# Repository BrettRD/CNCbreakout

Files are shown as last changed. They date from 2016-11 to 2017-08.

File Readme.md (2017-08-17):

# CNCbreakout

This is the working folder for the breakout board to wire the FPGA interface cards into the CNC cabinet.

The interfaces as described did not standardise voltages on the limit switches and left some signal poalrities up to chance

This board also has LED outputs showing the current state of all limits and home switches.

## PCB
There is a toner-transfer PCB in the compactus, but it requires about six hours of work fitting track jumpers.

The KiCad PCB simply has these as top-layer tracks. Export gerbers and buy PCBs; save your sanity.

## Documents:
There is no manual for the 220V X-axis servo controller. This repo contains the closest approximation, and seems to have the same menu and pinouts.

The pinouts for the interface cables currently only exist within the KiCad document.  Some of these will need to have piggyback connections.  With a bit of work and sanity checking, these pinouts can be converted to tables or PDF diagrams.

## Current Hardware:
The inactive X-axis motor has a fault in its signal lines pinout. This can be seen on the servo controller: navigate the menu to a live encoder display.  See the maxsineMotorpinout spreadsheet for the correct wiring.

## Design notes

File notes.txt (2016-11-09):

Estop handling is not required on this board.

Cables:
	Enable lines are routed via the breakout board
	Pinout not finalised
	DE15 and DE9 pcb connectors are by Oupiin available at altronics drawn from datasheet

PCB layout:
	Need to plan cable placement

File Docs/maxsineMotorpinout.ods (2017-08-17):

Signal | Motor Pin number | Colour | Diameter | Controller pin number
A+ | 4 | brown yellow | 0.25 | 1
A- | 7 | brown grey | 0.25 | 2
B+ | 5 | green brown | 0.25 | 3
B- | 8 | green black | 0.25 | 4
Z+ | 6 | white red | 0.14 | 5
Z- | 9 | white black | 0.14 | 6
U+ | 10 | black | 0.14 | 7
U- | 13 | brown | 0.14 | 8
V+ | 11 | orange | 0.14 | 9
V- | 14 | red | 0.14 | 10
W+ | 12 | green | 0.14 | 11
W- | 15 | yellow | 0.14 | 12
5v+ | 2 | brown red | 0.5 | 14
5v+ | 2 | brown red | 0.5 | 15
5v+ | 2 | brown red | 0.5 | 16
5v+ | 2 | brown red | 0.5 | 17
gnd | 3 | brown blue | 0.5 | 18
gnd | 3 | brown blue | 0.5 | 19
gnd | 3 | brown blue | 0.5 | 20
gnd | 3 | brown blue | 0.5 | 21
shield | 1 | shield |  | 26

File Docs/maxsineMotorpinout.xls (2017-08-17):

Signal | Motor Pin number | Colour | Diameter | Controller pin number
A+ | 4 | green | 0.25 | 1
A- | 7 | yellow | 0.25 | 2
B+ | 5 | orange | 0.25 | 3
B- | 8 | red | 0.25 | 4
Z+ | 6 | black | 0.14 | 5
Z- | 9 | brown | 0.14 | 6
U+ | 10 | brown yellow | 0.14 | 7
U- | 13 | brown grey | 0.14 | 8
V+ | 11 | green brown | 0.14 | 9
V- | 14 | green black | 0.14 | 10
W+ | 12 | white red | 0.14 | 11
W- | 15 | white black | 0.14 | 12
5v+ | 2 | brown red | 0.5 | 14
5v+ | 2 | brown red | 0.5 | 15
5v+ | 2 | brown red | 0.5 | 16
5v+ | 2 | brown red | 0.5 | 17
gnd | 3 | brown blue | 0.5 | 18
gnd | 3 | brown blue | 0.5 | 19
gnd | 3 | brown blue | 0.5 | 20
gnd | 3 | brown blue | 0.5 | 21
shield | 1 | shield |  | 26

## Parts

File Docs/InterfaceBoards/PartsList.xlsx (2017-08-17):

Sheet: 5i22_Baseboard Rev C x 2pcs
Ref | Value | Package | Manufacturer | Part Number | Element14 | Notes
C1 | 47uF | PANASONIC_D | Panasonic | EEEFK1C470P | 1850100
C2 | 100nF | C0805 | Multicomp | MC0603B104K500CT | 1759122 | 50V X7R dielectric 10%
C3 | 47uF | PANASONIC_D | Panasonic | EEEFK1C470P | 1850100
C4 | 100nF | C0805 | Multicomp | MC0603B104K500CT | 1759122 | 50V X7R dielectric 10%
C5 | 47uF | PANASONIC_D | Panasonic | EEEFK1C470P | 1850100
C6 | 100nF | C0805 | Multicomp | MC0603B104K500CT | 1759122 | 50V X7R dielectric 10%
C7 | 47uF | PANASONIC_D | Panasonic | EEEFK1C470P | 1850100
C8 | 100nF | C0805 | Multicomp | MC0603B104K500CT | 1759122 | 50V X7R dielectric 10%
C9 | 10nF | C1206 | Phycomp | CC1206KKX7RCBB103 | 1284146 | Must be 1000V
C10 | 47uF | PANASONIC_D | Panasonic | EEEFK1C470P | 1850100
C11 | 100nF | C0805 | Multicomp | MC0603B104K500CT | 1759122 | 50V X7R dielectric 10%
C12 | 47uF | PANASONIC_D | Panasonic | EEEFK1C470P | 1850100
C13 | 100nF | C0805 | Multicomp | MC0603B104K500CT | 1759122 | 50V X7R dielectric 10%
C14 | 100nF | C0805 | Multicomp | MC0603B104K500CT | 1759122 | 50V X7R dielectric 10%
C15 | 100nF | C0805 | Multicomp | MC0603B104K500CT | 1759122 | 50V X7R dielectric 10%
C16 | 100nF | C0805 | Multicomp | MC0603B104K500CT | 1759122 | 50V X7R dielectric 10%
C17 | 100nF | C0805 | Multicomp | MC0603B104K500CT | 1759122 | 50V X7R dielectric 10%
C18 | 100nF | C0805 | Multicomp | MC0603B104K500CT | 1759122 | 50V X7R dielectric 10%
C19 | 100nF | C0805 | Multicomp | MC0603B104K500CT | 1759122 | 50V X7R dielectric 10%
C20 | 1nF | C1206 | Multicomp | MC1206B102K102CT | 1855896 | Must be 1000V
C21 | 1nF | C1206 | Multicomp | MC1206B102K102CT | 1855896 | Must be 1000V
C22 | 1nF | C1206 | Multicomp | MC1206B102K102CT | 1855896 | Must be 1000V
C23 | 1nF | C1206 | Multicomp | MC1206B102K102CT | 1855896 | Must be 1000V
C24 | 1nF | C1206 | Multicomp | MC1206B102K102CT | 1855896 | Must be 1000V
C25 | 10nF | C1206 | Multicomp | MC1206B102K102CT | 1855896 | Must be 1000V
C26 | 1uF | C1206K | AVX | 12061C105KAT2A | 1657939 | > 50v preferred
C27 | 100nF | C0805 | Multicomp | MC0603B104K500CT | 1759122 | 50V X7R dielectric 10%
C28 | 100nF | C0805 | Multicomp | MC0603B104K500CT | 1759122 | 50V X7R dielectric 10%
C29 | 100nF | C0805 | Multicomp | MC0603B104K500CT | 1759122 | 50V X7R dielectric 10%
C30 | 100nF | C0805 | Multicomp | MC0603B104K500CT | 1759122 | 50V X7R dielectric 10%
C31 | 100nF | C0805 | Multicomp | MC0603B104K500CT | 1759122 | 50V X7R dielectric 10%
C32 | 100nF | C0805 | Multicomp | MC0603B104K500CT | 1759122 | 50V X7R dielectric 10%
C33 | 1nF | C1206 | Multicomp | MC1206B102K102CT | 1855896 | Must be 1000V
C34 | 1nF | C1206 | Multicomp | MC1206B102K102CT | 1855896 | Must be 1000V
C35 | 1nF | C1206 | Multicomp | MC1206B102K102CT | 1855896 | Must be 1000V
C36 | 1nF | C1206 | Multicomp | MC1206B102K102CT | 1855896 | Must be 1000V
C37 | 100nF | C0805 | Multicomp | MC0603B104K500CT | 1759122 | 50V X7R dielectric 10%
C38 | 100nF | C0805 | Multicomp | MC0603B104K500CT | 1759122 | 50V X7R dielectric 10%
D1 | GF1G | DO214AC | Vishay | GF1G-E3/5CA | 9549595
D2 | GF1G | DO214AC | Vishay | GF1G-E3/5CA | 9549595
D3 | GF1G | DO214AC | Vishay | GF1G-E3/5CA | 9549595
D4 | GF1G | DO214AC | Vishay | GF1G-E3/5CA | 9549595
D5 | GF1G | DO214AC | Vishay | GF1G-E3/5CA | 9549595
D6 |  | 1208-BI-COLOR | Dialight | 5988510207F | 1850756
IC1 | 74LVC32AD | SO14 | TI | SN74LVC32AD | 1102974
IC2 | 74LVC541ADW | SO20W | TI | 74LVC541ADW | 1470749
IC3 | 74LVC1G02DBV | SOT23-5 | TI | SN74LVC1G02DBVR | 1287579
IC4 | MC78M15CDT | TO252 | On Semi | MC78M15CDTG | 1211124
L1 | MPLCH0740L4R7 | 740 | Kemet | MPLCH0740L4R7 | 2364599
L2 | MPLCH0740L4R7 | 740 | Kemet | MPLCH0740L4R8 | 2364600
L3 | MPLCH0740L4R7 | 740 | Kemet | MPLCH0740L4R9 | 2364601
Q1 | STD30NF06L | TO252 | ST Micro | STD30NF06LT4 | 1752032
Q2 | STD30NF06L | TO252 | ST Micro | STD30NF06LT5 | 1752033
Q3 | MUN2211T1 | SC59-BEC | On Semi | MUN2211T1G | 1232166
Q4 | MUN2211T1 | SC59-BEC | On Semi | MUN2211T1G | 1232166
Q5 | STD30NF06L | TO252 | ST Micro | STD30NF06LT5 | 1752033
Q6 | STD30NF06L | TO252 | ST Micro | STD30NF06LT5 | 1752033
Q7 | STD30NF06L | TO252 | ST Micro | STD30NF06LT5 | 1752033
Q8 | MUN2211T1 | SC59-BEC | On Semi | MUN2211T1G | 1232166
Q9 | MUN2211T1 | SC59-BEC | On Semi | MUN2211T1G | 1232166
Q10 | MUN2211T1 | SC59-BEC | On Semi | MUN2211T1G | 1232166
R1 | 1M | R1206 |  |  |  | 5% 1206 case
R2 | 51R | R0805 |  |  |  | 1% 0.125W 0805 case
R3 | 51R | R0805 |  |  |  | 1% 0.125W 0805 case
R4 | 51R | R0805 |  |  |  | 1% 0.125W 0805 case
R5 | 51R | R0805 |  |  |  | 1% 0.125W 0805 case
R6 | 0R | R0805 |  |  |  | 1% 0.125W 0805 case
R7 | 0R | R0805 |  |  |  | 1% 0.125W 0805 case
R8 | 10k | R0805 |  |  |  | 1% 0.125W 0805 case
R9 | 10k | R0805 |  |  |  | 1% 0.125W 0805 case
R10 | 10k | R0805 |  |  |  | 1% 0.125W 0805 case
R11 | 10k | R0805 |  |  |  | 1% 0.125W 0805 case
R12 | 220R | R0805 |  |  |  | 1% 0.125W 0805 case
R13 | 220R | R0805 |  |  |  | 1% 0.125W 0805 case
R14 | 1M | R1206 |  |  |  | 5% 1206 case
R15 | 220R | R0805 |  |  |  | 1% 0.125W 0805 case
R16 | 220R | R0805 |  |  |  | 1% 0.125W 0805 case
R17 | 220R | R0805 |  |  |  | 1% 0.125W 0805 case
R18 | 1k | R0805 |  |  |  | 1% 0.125W 0805 case
R19 | 1k | R0805 |  |  |  | 1% 0.125W 0805 case
R20 | 2K | R0805 |  |  |  | 1% 0.125W 0805 case
R21 | 51R | R0805 |  |  |  | 1% 0.125W 0805 case
R22 | 2K | R0805 |  |  |  | 1% 0.125W 0805 case
R23 | 330R | R0805 |  |  |  | 1% 0.125W 0805 case
R24 | 270R | R0805 |  |  |  | 1% 0.125W 0805 case
U1 | SN74LVC2G14DBV | SOT23-6 | TI | SN74LVC2G14DBVR | 1470884
U2 | SN74LVC1G19DBV | SOT23-6 | TI | SN74LVC1G19DBVR | 2334936
U3 | SN74LVC2G14DBV | SOT23-6 | TI | SN74LVC2G14DBVR | 1470884
U4 | ACPL-302P | SO-6(P) | Avago | ACPL-P302-000E | 1640555 | Can use ACPL-P314-000E as an alternative (Element14 : 1640556)
U5 | ACPL-302P | SO-6(P) | Avago | ACPL-P302-000E | 1640555 | Can use ACPL-P314-000E as an alternative (Element14 : 1640556)
U6 | ACPL-302P | SO-6(P) | Avago | ACPL-P302-000E | 1640555 | Can use ACPL-P314-000E as an alternative (Element14 : 1640556)
U7 | ACPL-302P | SO-6(P) | Avago | ACPL-P302-000E | 1640555 | Can use ACPL-P314-000E as an alternative (Element14 : 1640556)
U8 | ACPL-302P | SO-6(P) | Avago | ACPL-P302-000E | 1640555 | Can use ACPL-P314-000E as an alternative (Element14 : 1640556)
U9 | SN74LVC2G14DBV | SOT23-6 | TI | SN74LVC2G14DBVR | 1470884
U10 | HCPL-263L | SO-8 | Avago | HCPL-263L-300E | 1085053
X1 | 2550- | PAK100/2500-50 | AMP | T821150A1S100CEU | 2215315 | Any alternative is OK
X2 | 2550- | PAK100/2500-50 | AMP | T821150A1S100CEU | 2215315 | Any alternative is OK
X3 | 641737 | 641737 | TE Connectivity | 1-641737-1 | 6478712 | Molex MATE-N-LOK hard disk connector
X4 |  | PAK100/2500-F-16 | TE Connectivity | 215307-8 | 3419241 | Any alternative is OK
X5 |  | PAK100/2500-F-16 | TE Connectivity | 215307-8 | 3419241 | Any alternative is OK
X6 | 2514-F | PAK100/2500-F-14 | TE Connectivity | 215307-7 | 3419230 | Any alternative is OK
X7 |  | PAK100/2500-F-16 | TE Connectivity | 215307-8 | 3419241 | Any alternative is OK
X8 |  | PAK100/2500-F-16 | TE Connectivity | 215307-8 | 3419241 | Any alternative is OK
X9 |  | PHOENIXCONTACT_MSTBA_508_7 | Phoenix Contact | MSTBA 2,5/ 7-G-5,08-LR | 2315187 | Get some of the screw terminal mating halves as well.
X10 |  | PHOENIXCONTACT_MSTBA-508_5 | Phoenix Contact | MSTBA 2,5/ 5-G-5,08-LR | 2315185 | Get some of the screw terminal mating halves as well.

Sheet: ACS806 Rev C x 4pcs
Ref | Value | Package | Manufacturer | Part Number | Element14 | Notes
C1 | 100nF | C0805 | Multicomp | MC0603B104K500CT | 1759122 | 50V X7R dielectric 10%
C2 | 100nF | C0805 | Multicomp | MC0603B104K500CT | 1759122 | 50V X7R dielectric 10%
C3 | 47uF | PANASONIC_C | Panasonic | EEEFK0J470R | 1850084 | Minimum 4v
C4 | 100nF | C0805 | Multicomp | MC0603B104K500CT | 1759122 | 50V X7R dielectric 10%
C5 | 22uF | PANASONIC_C | Panasonic | EEEFK1E220AR | 1244411 | Minimum 16v
C6 | 100nF | C0805 | Multicomp | MC0603B104K500CT | 1759122 | 50V X7R dielectric 10%
C7 | 100nF | C0805 | Multicomp | MC0603B104K500CT | 1759122 | 50V X7R dielectric 10%
C8 | 100nF | C0805 | Multicomp | MC0603B104K500CT | 1759122 | 50V X7R dielectric 10%
C9 | 100nF | C0805 | Multicomp | MC0603B104K500CT | 1759122 | 50V X7R dielectric 10%
C10 | 100nF | C0805 | Multicomp | MC0603B104K500CT | 1759122 | 50V X7R dielectric 10%
C11 | 100nF | C0805 | Multicomp | MC0603B104K500CT | 1759122 | 50V X7R dielectric 10%
C12 | 100nF | C0805 | Multicomp | MC0603B104K500CT | 1759122 | 50V X7R dielectric 10%
LED1 |  | CHIP-LED0805 | Multicomp | 703-0104 | 2112116 | green
LED2 |  | CHIP-LED0805 | Multicomp | 703-0107 | 2112119 | red
LED3 |  | CHIP-LED0805 | Multicomp | 703-0105 | 2112117 | yellow
R1 | 1K | R1206 |  |  |  | 1% 0.25W 1206 case
R2 | 1K | R1206 |  |  |  | 1% 0.25W 1206 case
R3 | 1K | R1206 |  |  |  | 1% 0.25W 1206 case
R4 | 10k | R0805 |  |  |  | 1% 0.125W 0805 case
R5 | 51R | R0805 |  |  |  | 1% 0.125W 0805 case
R6 | 270R | R0805 |  |  |  | 1% 0.125W 0805 case
R7 | 10k | R0805 |  |  |  | 1% 0.125W 0805 case
R8 | 51R | R0805 |  |  |  | 1% 0.125W 0805 case
R9 | 270R | R0805 |  |  |  | 1% 0.125W 0805 case
R10 | 330R | R0805 |  |  |  | 1% 0.125W 0805 case
R11 | 1K | R0805 |  |  |  | 1% 0.125W 0805 case
R12 | 470R | R0805 |  |  |  | 1% 0.125W 0805 case
R13 | 470R | R0805 |  |  |  | 1% 0.125W 0805 case
R14 | 470R | R0805 |  |  |  | 1% 0.125W 0805 case
R15 | 470R | R0805 |  |  |  | 1% 0.125W 0805 case
R16 | 470R | R0805 |  |  |  | 1% 0.125W 0805 case
R17 | 470R | R0805 |  |  |  | 1% 0.125W 0805 case
R18 | 470R | R0805 |  |  |  | 1% 0.125W 0805 case
R19 | 270R | R0805 |  |  |  | 1% 0.125W 0805 case
R20 | 51R | R0805 |  |  |  | 1% 0.125W 0805 case
R21 | 270R | R0805 |  |  |  | 1% 0.125W 0805 case
R22 | 51R | R0805 |  |  |  | 1% 0.125W 0805 case
R23 | 270R | R0805 |  |  |  | 1% 0.125W 0805 case
R24 | 51R | R0805 |  |  |  | 1% 0.125W 0805 case
R25 | 2K | R0805 |  |  |  | 1% 0.125W 0805 case
R26 | 51R | R0805 |  |  |  | 1% 0.125W 0805 case
R27 | 270R | R0805 |  |  |  | 1% 0.125W 0805 case
R28 | 51R | R0805 |  |  |  | 1% 0.125W 0805 case
R29 | 270R | R0805 |  |  |  | 1% 0.125W 0805 case
R30 | 51R | R0805 |  |  |  | 1% 0.125W 0805 case
U1 | AEIC-2631-S16 | SO16 | Avago | AEIC-2631-S16 | 2447896
U2 | ACPL-217 | SO-4 | Avago | ACPL-217-50AE | 1602616
U3 | SN74LVC2G14DBV | SOT23-6 | TI | SN74LVC2G14DBVR | 1470884
U4 | ACPL-217 | SO-4 | Avago | ACPL-217-50AE | 1602616
U5 | SN74LVC2G14DBV | SOT23-6 | TI | SN74LVC2G14DBVR | 1470884
U6 | HCPL-263L | SO-8 | Avago | HCPL-263L-300E | 1085053
U7 | SN74LVC2G14DBV | SOT23-6 | TI | SN74LVC2G14DBVR | 1470884
U8 | HCPL-263L | SO-8 | Avago | HCPL-263L-300E | 1085053
U9 | SN74LVC2G14DBV | SOT23-6 | TI | SN74LVC2G14DBVR | 1470884
U10 | HCPL-263L | SO-8 | Avago | HCPL-263L-300E | 1085053
X1 | 2516-5 | PAK100/2500-5-16 | TE Connectivity | 1-1634689-6 | 8396019
X2 | ACS806 | HDM26H | AMP | L717HDA26PD1CH4F | 2401148

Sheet: PowerFlex525 RevC x 2pcs
Ref | Value | Package | Manufacturer | Part Number | Element14 | Notes
C1 | 100nF | C0805 | Multicomp | MC0603B104K500CT | 1759122 | 50V X7R dielectric 10%
C2 | 100uF | PANASONIC_C | Panasonic | EEEFK0J101UR | 1850085
C3 | 100nF | C0805 | Multicomp | MC0603B104K500CT | 1759122 | 50V X7R dielectric 10%
C4 | 100nF | C0805 | Multicomp | MC0603B104K500CT | 1759123 | 50V X7R dielectric 10%
C5 | 100nF | C0805 | Multicomp | MC0603B104K500CT | 1759124 | 50V X7R dielectric 10%
C6 | 100nF | C0805 | Multicomp | MC0603B104K500CT | 1759125 | 50V X7R dielectric 10%
C7 | 100nF | C0805 | Multicomp | MC0603B104K500CT | 1759126 | 50V X7R dielectric 10%
C8 | 100nF | C0805 | Multicomp | MC0603B104K500CT | 1759127 | 50V X7R dielectric 10%
C9 | 100nF | C0805 | Multicomp | MC0603B104K500CT | 1759128 | 50V X7R dielectric 10%
C10 | 100nF | C0805 | Multicomp | MC0603B104K500CT | 1759129 | 50V X7R dielectric 10%
C11 | 47nF | C0805 | Kemet | C0805C473J3GACTU | 1535570 | NP0/C0G dialectric 5%
C12 | 4n7 | C0805 | Kemet | C0805C472J2GACAUTO | 2426891 | NP0/C0G dialectric 5%
C13 | 1uF | C1206K | AVX | 12061C105KAT2A | 1657939 | > 50v preferred
C14 | 100nF | C0805 | Multicomp | MC0603B104K500CT | 1759129 | 50V X7R dielectric 10%
C15 | 100nF | C0805 | Multicomp | MC0603B104K500CT | 1759129 | 50V X7R dielectric 10%
D1 | SMBJ36A | SMBG | Bourns | SMBJ36A | 1899470 | 36V TVS
D2 | BAV199 | SOT23 | On Semi | BAV199LT1G | 1431115
D3 | BAV199 | SOT23 | On Semi | BAV199LT1G | 1431116
LED1 |  | CHIP-LED0805 | Multicomp | 703-0104 | 2112116 | green
LED2 |  | CHIP-LED0805 | Multicomp | 703-0105 | 2112117 | yellow
Q1 | MUN2211T1 | SC59-BEC | On Semi | MUN2211T1G | 1232166
Q2 | MUN2211T1 | SC59-BEC | On Semi | MUN2211T1G | 1232167
Q3 | MUN2211T1 | SC59-BEC | On Semi | MUN2211T1G | 1232168
Q4 | MUN2211T1 | SC59-BEC | On Semi | MUN2211T1G | 1232169
Q5 | MUN2211T1 | SC59-BEC | On Semi | MUN2211T1G | 1232170
Q6 | MUN2211T1 | SC59-BEC | On Semi | MUN2211T1G | 1232171
R1 | 10k | R0805 |  |  |  | 1% 0.125W 0805 case
R2 | 51R | R0805 |  |  |  | 1% 0.125W 0805 case
R3 | 10k | R0805 |  |  |  | 1% 0.125W 0805 case
R4 | 51R | R0805 |  |  |  | 1% 0.125W 0805 case
R5 | 330R | R0805 |  |  |  | 1% 0.125W 0805 case
R6 | 2K2 | R0805 |  |  |  | 1% 0.125W 0805 case
R7 | 220R | R0805 |  |  |  | 1% 0.125W 0805 case
R8 | 220R | R0805 |  |  |  | 1% 0.125W 0805 case
R9 | 220R | R0805 |  |  |  | 1% 0.125W 0805 case
R10 | 220R | R0805 |  |  |  | 1% 0.125W 0805 case
R11 | 220R | R0805 |  |  |  | 1% 0.125W 0805 case
R12 | 220R | R0805 |  |  |  | 1% 0.125W 0805 case
R13 | 220R | R0805 |  |  |  | 1% 0.125W 0805 case
R14 | 20k | R0805 |  |  |  | 1% 0.125W 0805 case
R15 | 10k | R0805 |  |  |  | 1% 0.125W 0805 case
R16 | 100k | R0805 |  |  |  | 1% 0.125W 0805 case
T1 | MJD31 | DPAK | On Semi | MJD31CT4G | 2317563
U1 | SN74LVC2G17DBV | SOT23-6 | TI | SN74LVC2G17DBVR | 1470776
U2 | ACPL-302P | SO-6(P) | Avago | ACPL-P302-000E | 1640555 | Can use ACPL-P314-000E as an alternative (Element14 : 1640556)
U3 | ACPL-302P | SO-6(P) | Avago | ACPL-P302-000E | 1640556 | Can use ACPL-P314-000E as an alternative (Element14 : 1640556)
U4 | ACPL-302P | SO-6(P) | Avago | ACPL-P302-000E | 1640557 | Can use ACPL-P314-000E as an alternative (Element14 : 1640556)
U5 | ACPL-302P | SO-6(P) | Avago | ACPL-P302-000E | 1640558 | Can use ACPL-P314-000E as an alternative (Element14 : 1640556)
U6 | ACPL-302P | SO-6(P) | Avago | ACPL-P302-000E | 1640559 | Can use ACPL-P314-000E as an alternative (Element14 : 1640556)
U7 | ACPL-302P | SO-6(P) | Avago | ACPL-P302-000E | 1640560 | Can use ACPL-P314-000E as an alternative (Element14 : 1640556)
U8 | TLV2371DBV | SOT23-5 | TI | TLV2371IDBVT | 8454990
U9 | ACPL-302P | SO-6(P) | Avago | ACPL-P302-000E | 1640560 | Can use ACPL-P314-000E as an alternative (Element14 : 1640556)
U10 | XTR117DGK | MSOP8 | TI | XTR117AIDGKT | 2323371
X1 | 2514-5 | PAK100/2500-5-14 | TE Connectivity | 1-1634689-4 | 8396000
X2 |  | HDM15H | AMP | L717HDE15PD1CH4R | 2401160

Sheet: KRS Rev C x 4pcs
Ref | Value | Package | Manufacturer | Part Number | Element14 | Notes
C1 | 100nF | C0805 | Multicomp | MC0603B104K500CT | 1759122 | 50V X7R dielectric 10%
C2 | 100nF | C0805 | Multicomp | MC0603B104K500CT | 1759122 | 50V X7R dielectric 10%
C3 | 47uF | PANASONIC_C | Panasonic | EEEFK0J470R | 1850084 | Minimum 4v
C4 | 100nF | C0805 | Multicomp | MC0603B104K500CT | 1759122 | 50V X7R dielectric 10%
C5 | 22uF | PANASONIC_C | Panasonic | EEEFK1E220AR | 1244411 | Minimum 6v3
C6 | 100nF | C0805 | Multicomp | MC0603B104K500CT | 1759122 | 50V X7R dielectric 10%
C7 | 100nF | C0805 | Multicomp | MC0603B104K500CT | 1759122 | 50V X7R dielectric 10%
C8 | 100nF | C0805 | Multicomp | MC0603B104K500CT | 1759122 | 50V X7R dielectric 10%
C9 | 100nF | C0805 | Multicomp | MC0603B104K500CT | 1759122 | 50V X7R dielectric 10%
C10 | 100nF | C0805 | Multicomp | MC0603B104K500CT | 1759122 | 50V X7R dielectric 10%
C11 | 100nF | C0805 | Multicomp | MC0603B104K500CT | 1759122 | 50V X7R dielectric 10%
LED1 |  | CHIP-LED0805 | Multicomp | 703-0104 | 2112116 | green
LED2 |  | CHIP-LED0805 | Multicomp | 703-0104 | 2112116 | green
R1 | 270R | R0805 |  |  |  | 1% 0.125W 0805 case
R2 | 51R | R0805 |  |  |  | 1% 0.125W 0805 case
R3 | 51R | R0805 |  |  |  | 1% 0.125W 0805 case
R4 | 51R | R0805 |  |  |  | 1% 0.125W 0805 case
R5 | 10k | R0805 |  |  |  | 1% 0.125W 0805 case
R6 | 51R | R0805 |  |  |  | 1% 0.125W 0805 case
R7 | 2K | R0805 |  |  |  | 1% 0.125W 0805 case
R8 | 330R | R0805 |  |  |  | 1% 0.125W 0805 case
R9 | 2K | R0805 |  |  |  | 1% 0.125W 0805 case
R10 | 10k | R0805 |  |  |  | 1% 0.125W 0805 case
R11 | 51R | R0805 |  |  |  | 1% 0.125W 0805 case
R12 | 2K | R0805 |  |  |  | 1% 0.125W 0805 case
R13 | 470R | R0805 |  |  |  | 1% 0.125W 0805 case
R14 | 470R | R0805 |  |  |  | 1% 0.125W 0805 case
R15 | 470R | R0805 |  |  |  | 1% 0.125W 0805 case
R16 | 470R | R0805 |  |  |  | 1% 0.125W 0805 case
R17 | 470R | R0805 |  |  |  | 1% 0.125W 0805 case
R18 | 470R | R0805 |  |  |  | 1% 0.125W 0805 case
R19 | 270R | R0805 |  |  |  | 1% 0.125W 0805 case
R20 | 51R | R0805 |  |  |  | 1% 0.125W 0805 case
R21 | 270R | R0805 |  |  |  | 1% 0.125W 0805 case
R22 | 51R | R0805 |  |  |  | 1% 0.125W 0805 case
R23 | 270R | R0805 |  |  |  | 1% 0.125W 0805 case
R24 | 51R | R0805 |  |  |  | 1% 0.125W 0805 case
R25 | 51R | R0805 |  |  |  | 1% 0.125W 0805 case
R26 | 2K | R0805 |  |  |  | 1% 0.125W 0805 case
R27 | 51R | R0805 |  |  |  | 1% 0.125W 0805 case
R28 | 2K | R0805 |  |  |  | 1% 0.125W 0805 case
R29 | 51R | R0805 |  |  |  | 1% 0.125W 0805 case
R30 | 2K | R0805 |  |  |  | 1% 0.125W 0805 case
U1 | AEIC-2631-S16 | SO16 | Avago | AEIC-2631-S16 | 2447896
U2 | ACPL-217 | SO-4 | Avago | ACPL-217-50AE | 1602616
U3 | ACPL-217 | SO-4 | Avago | ACPL-217-50AE | 1602616
U4 | SN74LVC2G14DBV | SOT23-6 | TI | SN74LVC2G14DBVR | 1470884
U5 | ACPL-217 | SO-4 | Avago | ACPL-217-50AE | 1602616
U6 | SN74LVC2G14DBV | SOT23-6 | TI | SN74LVC2G14DBVR | 1470884
U7 | HCPL-263L | SO-8 | Avago | HCPL-263L-300E | 1085053
U8 | SN74LVC2G14DBV | SOT23-6 | TI | SN74LVC2G14DBVR | 1470884
U9 | HCPL-263L | SO-8 | Avago | HCPL-263L-300E | 1085053
U10 | SN74LVC2G14DBV | SOT23-6 | TI | SN74LVC2G14DBVR | 1470884
U11 | ACPL-217 | SO-4 | Avago | ACPL-217-50AE | 1602616
U12 | ACPL-217 | SO-4 | Avago | ACPL-217-50AE | 1602616
X1 | 2516-5 | PAK100/2500-5-16 | TE Connectivity | 1-1634689-6 | 8396019
X2 |  | M25HP | AMP | L717HDA26PD1CH4F | 2401148

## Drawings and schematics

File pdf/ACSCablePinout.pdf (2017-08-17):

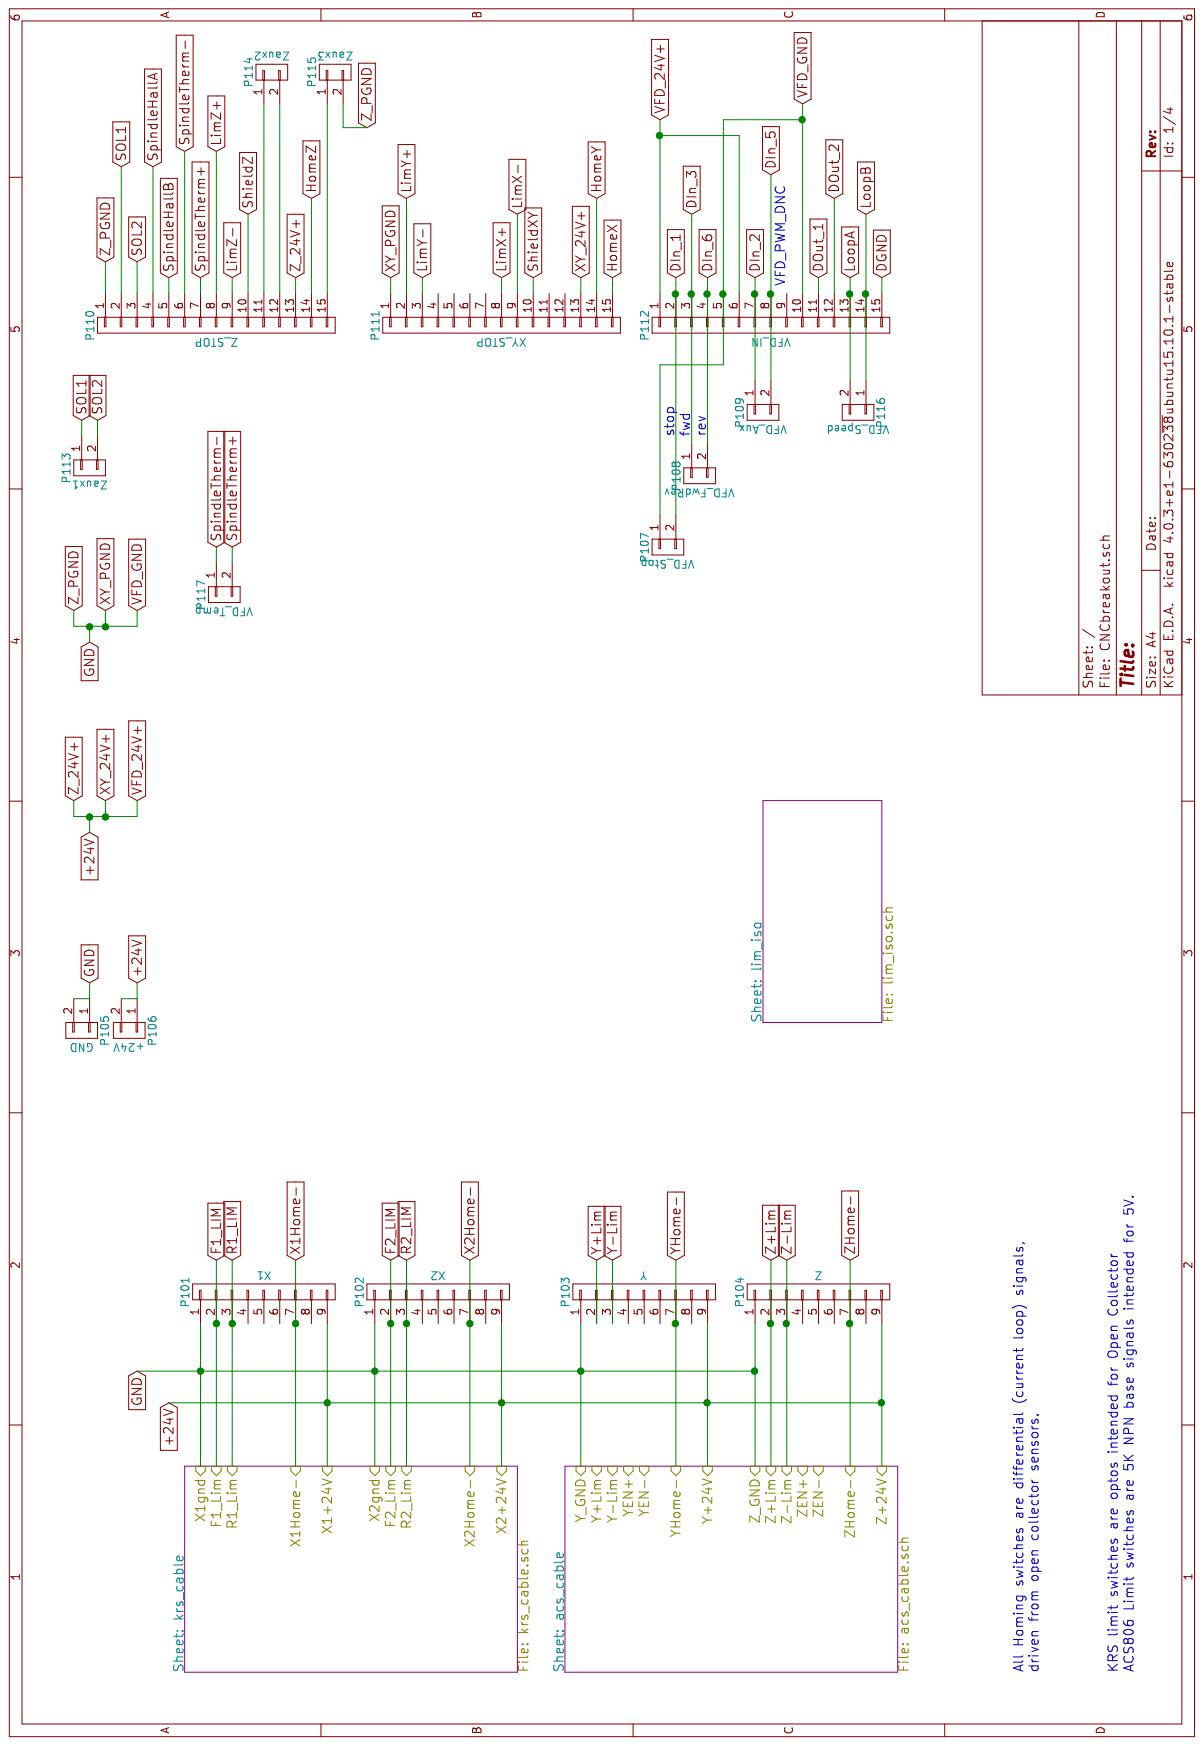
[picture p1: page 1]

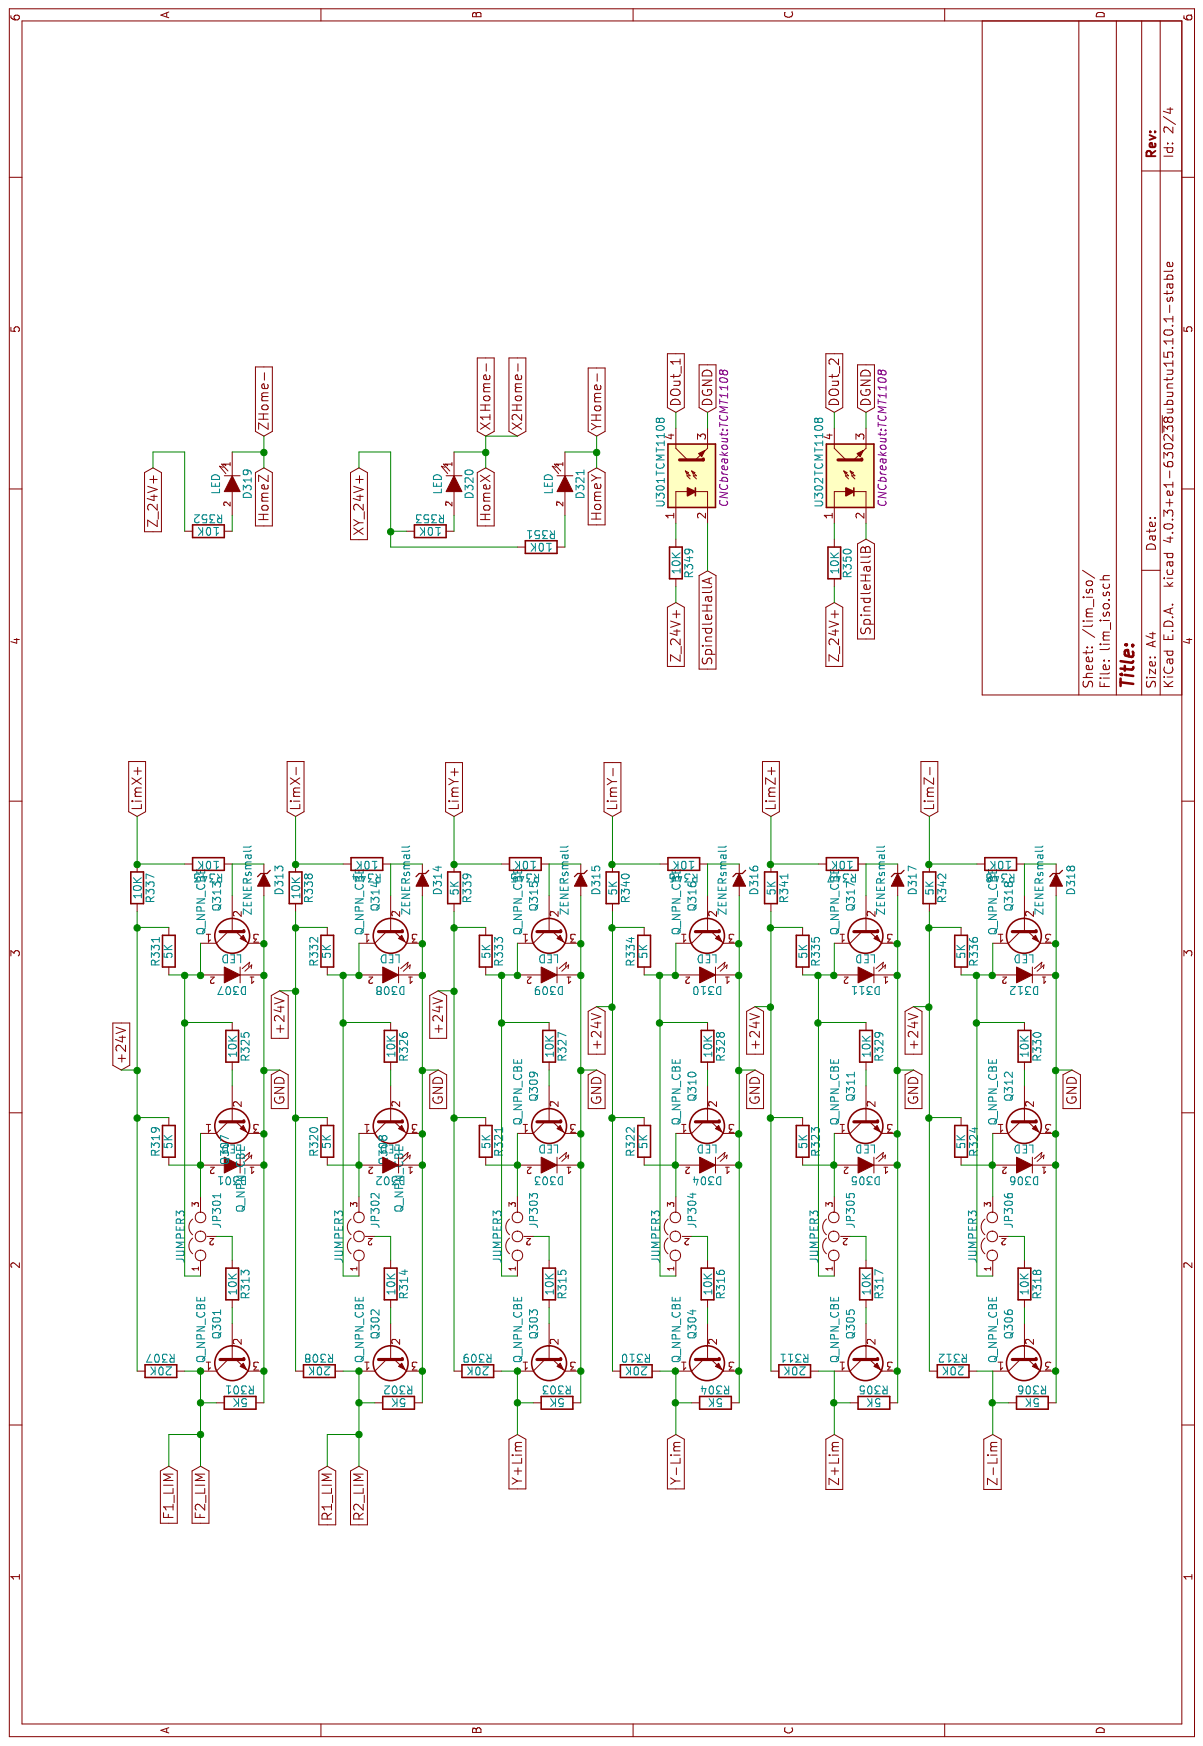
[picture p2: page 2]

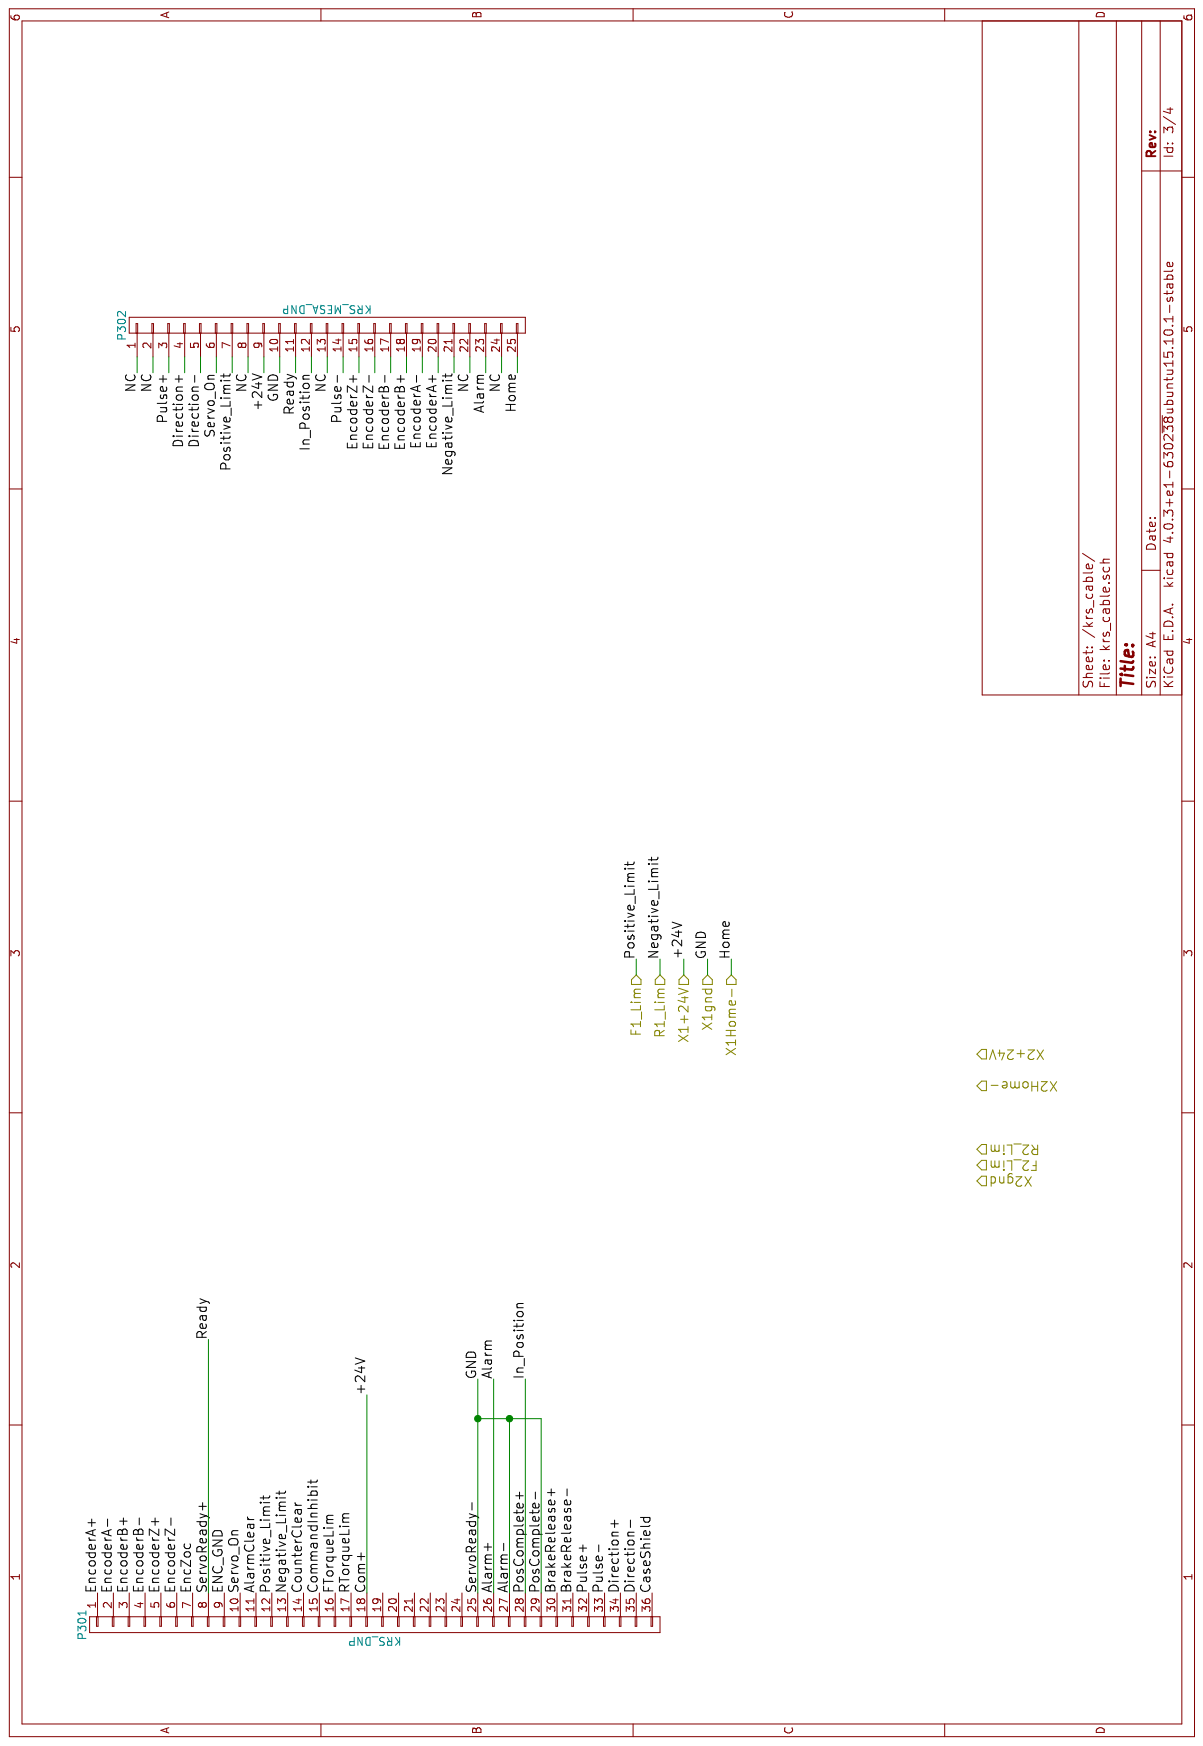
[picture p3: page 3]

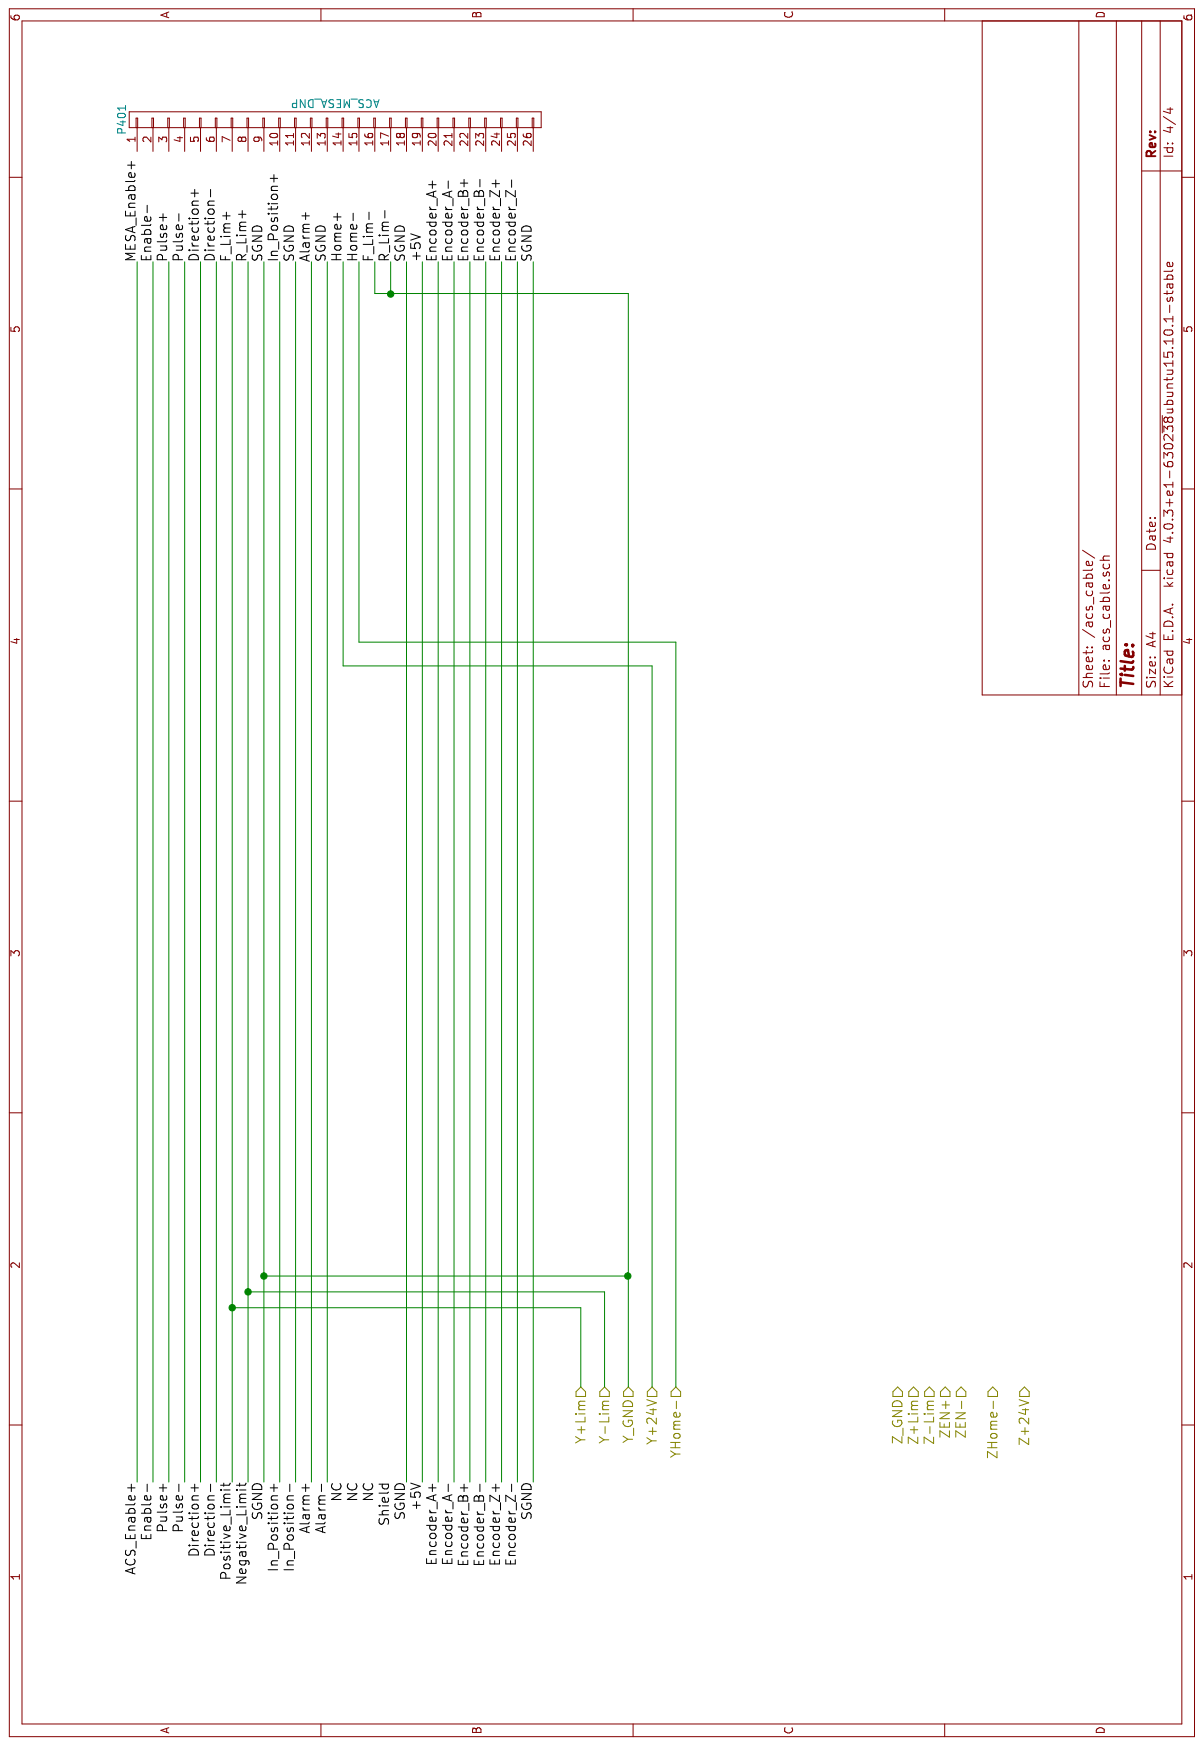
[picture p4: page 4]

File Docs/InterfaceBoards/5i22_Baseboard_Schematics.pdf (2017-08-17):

2550- | 2550-
X1-1 | X1-2

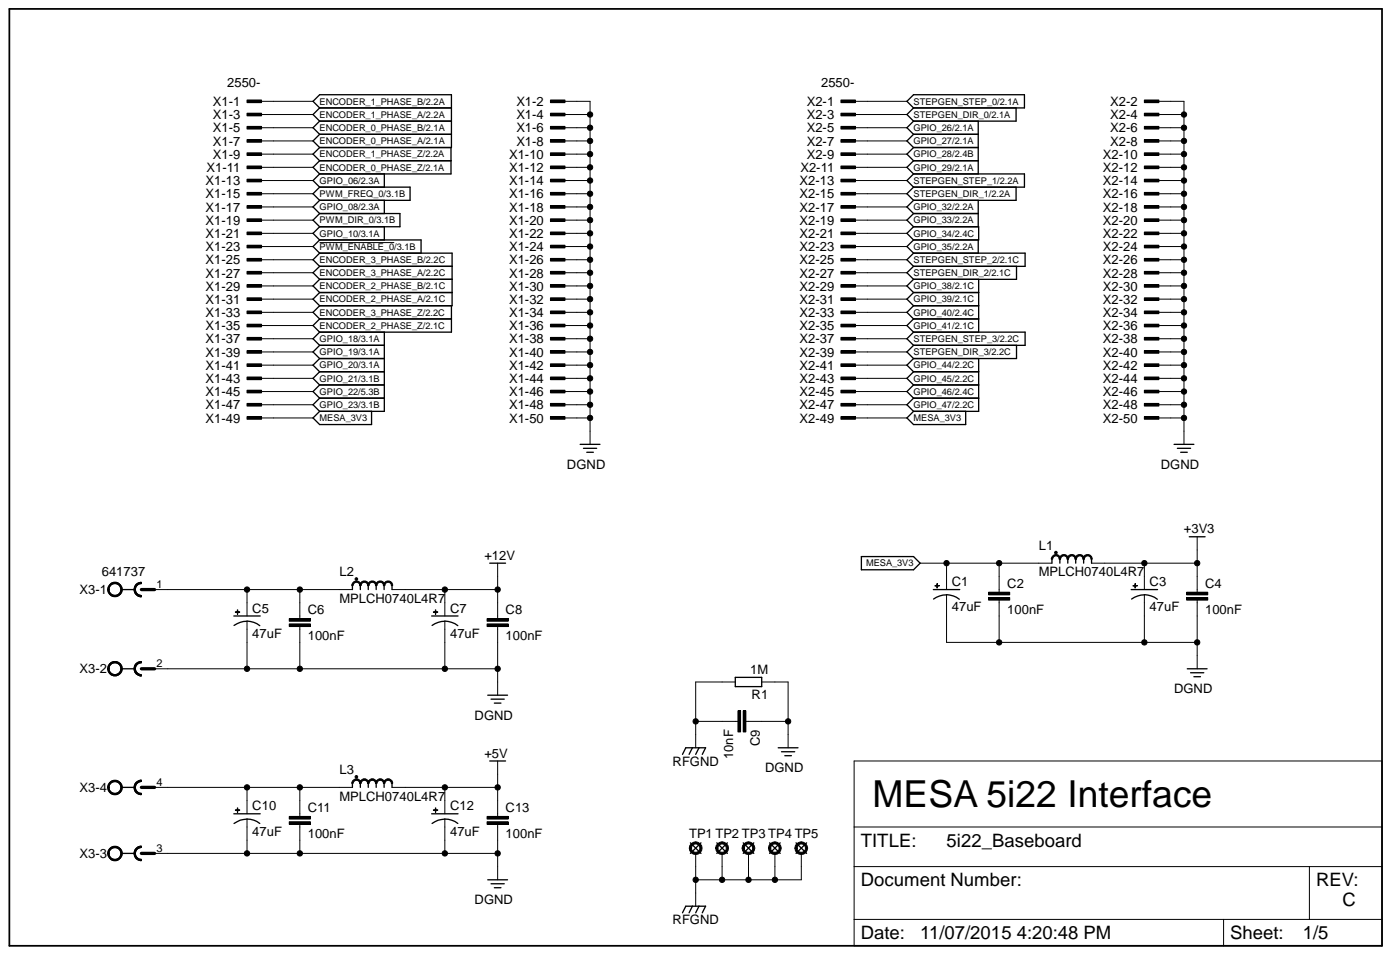
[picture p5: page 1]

Document Number: | REV: C

Date: 11/07/2015 4:20:48 PM | Sheet: 1/5

2514-F

+5V

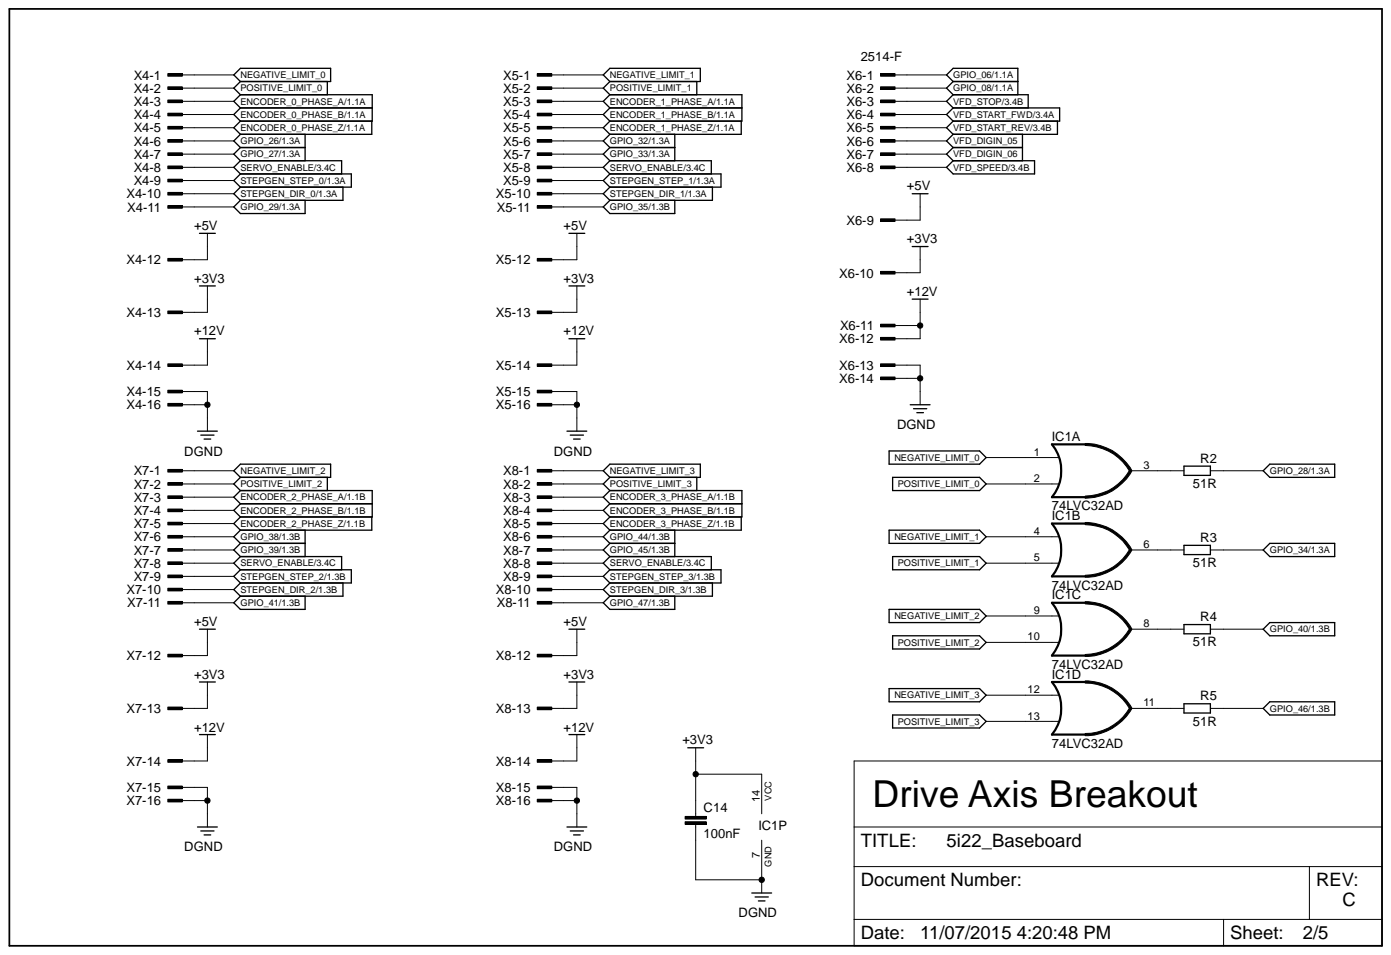
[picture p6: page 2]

Document Number: | REV: C

Date: 11/07/2015 4:20:48 PM | Sheet: 2/5

+3V3

## SN74LVC2G14DBV

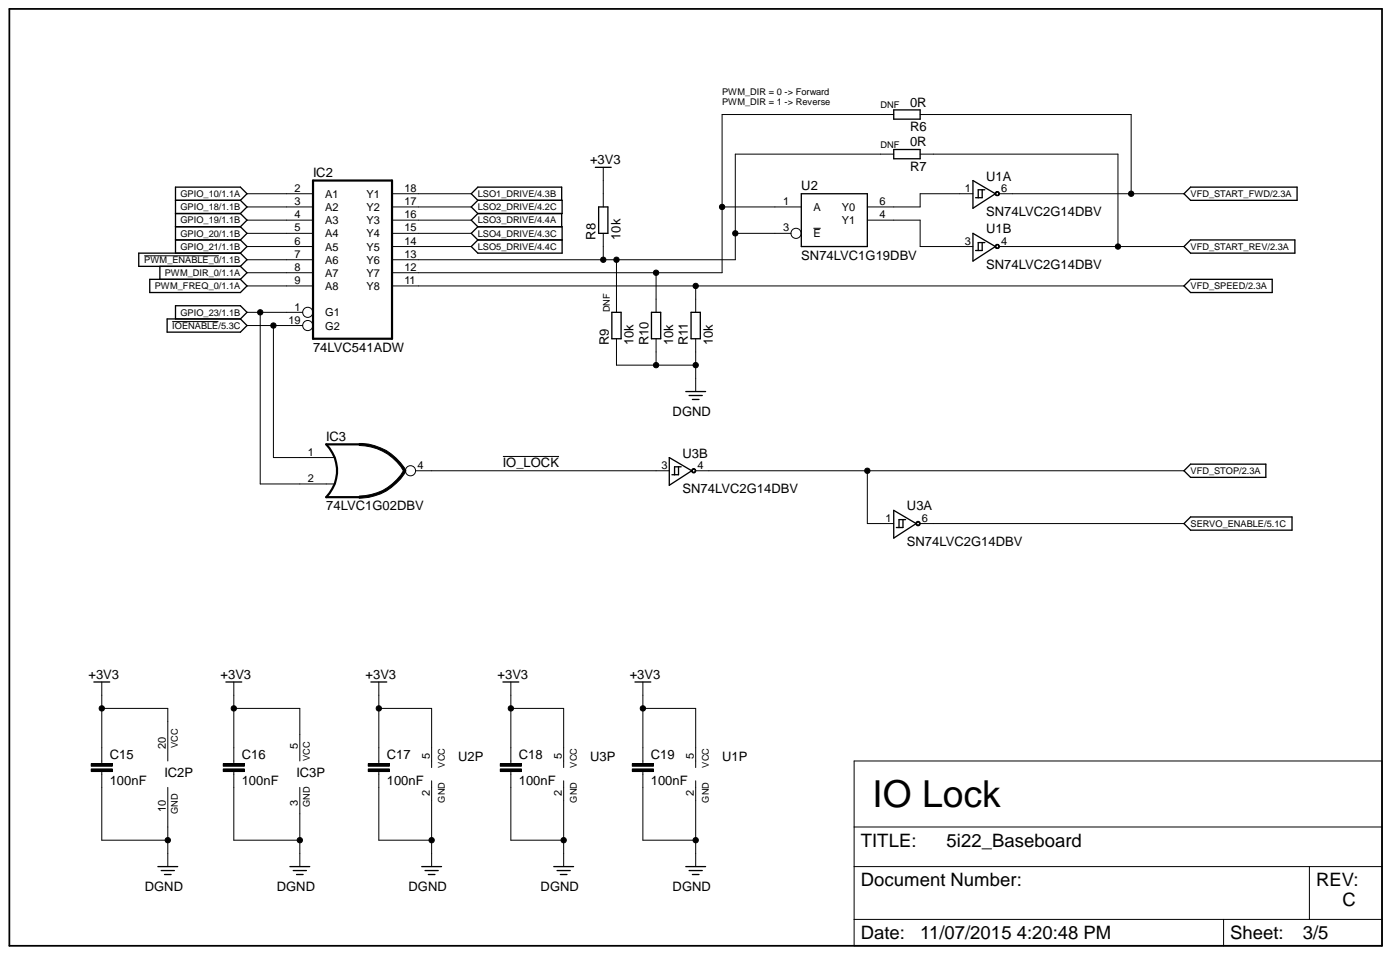
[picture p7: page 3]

## STD30NF06L

## GF1G

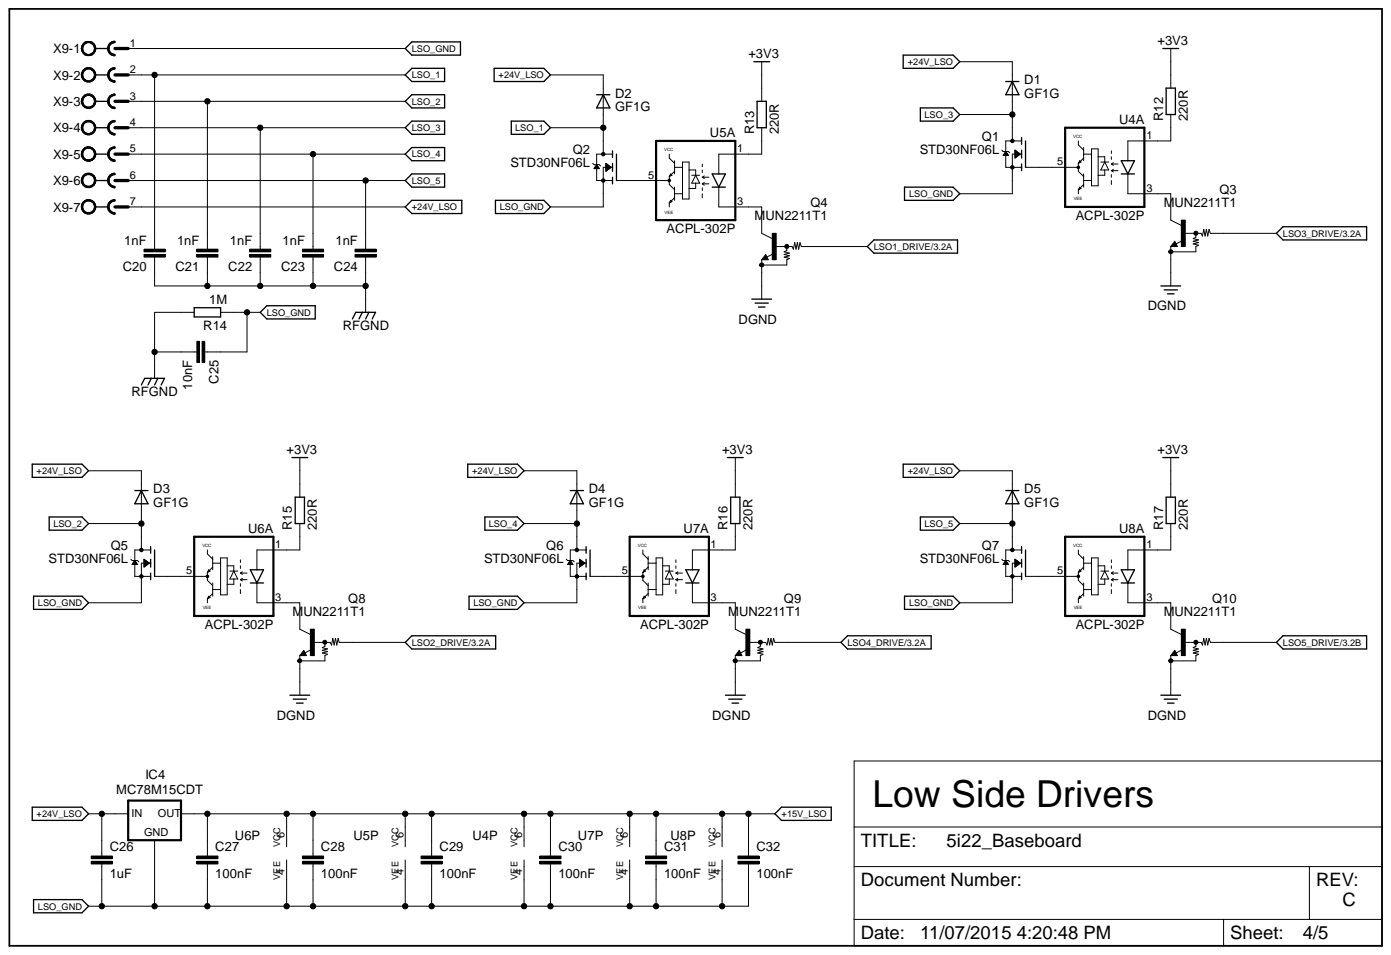
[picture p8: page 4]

Document Number: | REV: C

Date: 11/07/2015 4:20:48 PM | Sheet: 4/5

1nF | 1nF | 1nF | 1nF
X10-1 | 1

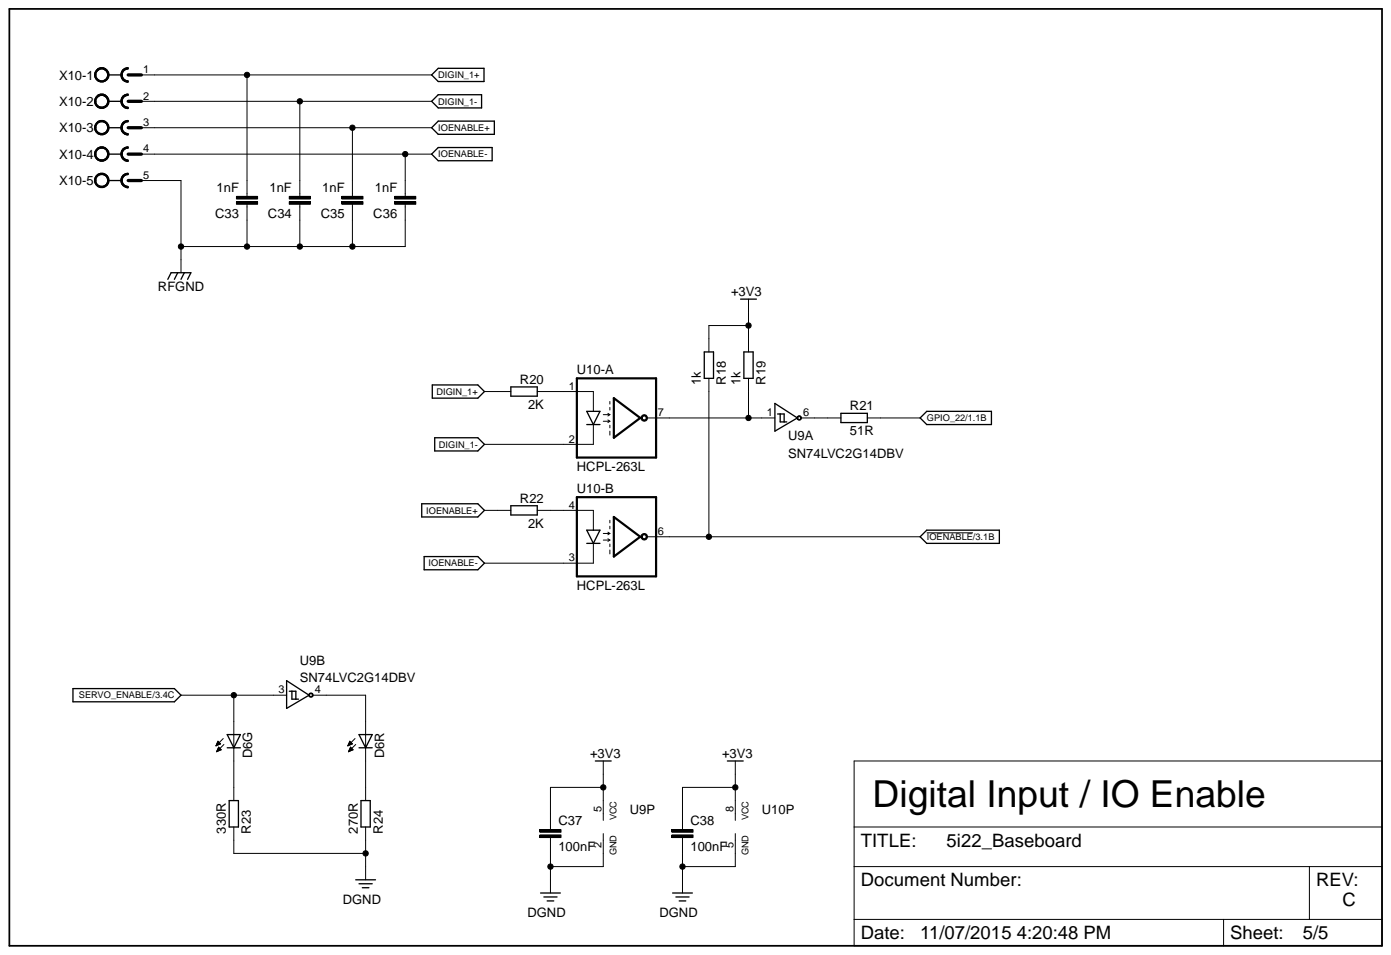
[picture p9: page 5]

Digital Input / IO Enable

Document Number: | REV: C

Date: 11/07/2015 4:20:48 PM | Sheet: 5/5

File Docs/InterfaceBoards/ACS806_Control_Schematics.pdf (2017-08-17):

2516-5

## AEIC-2631-S16

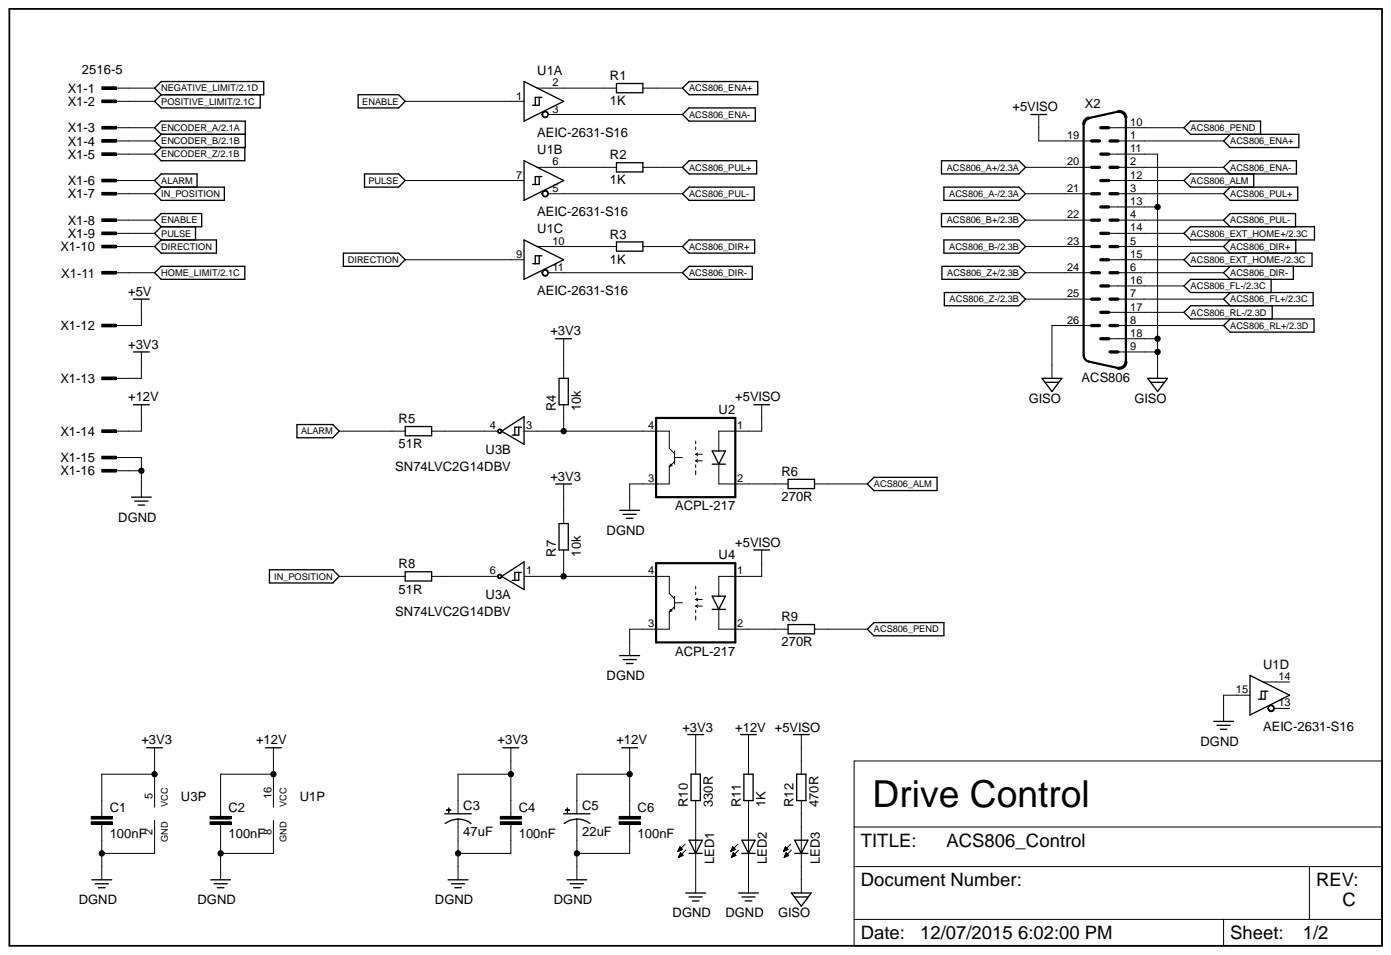
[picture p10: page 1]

Document Number: | REV: C

Date: 12/07/2015 6:02:00 PM | Sheet: 1/2

## HCPL-263L

270R

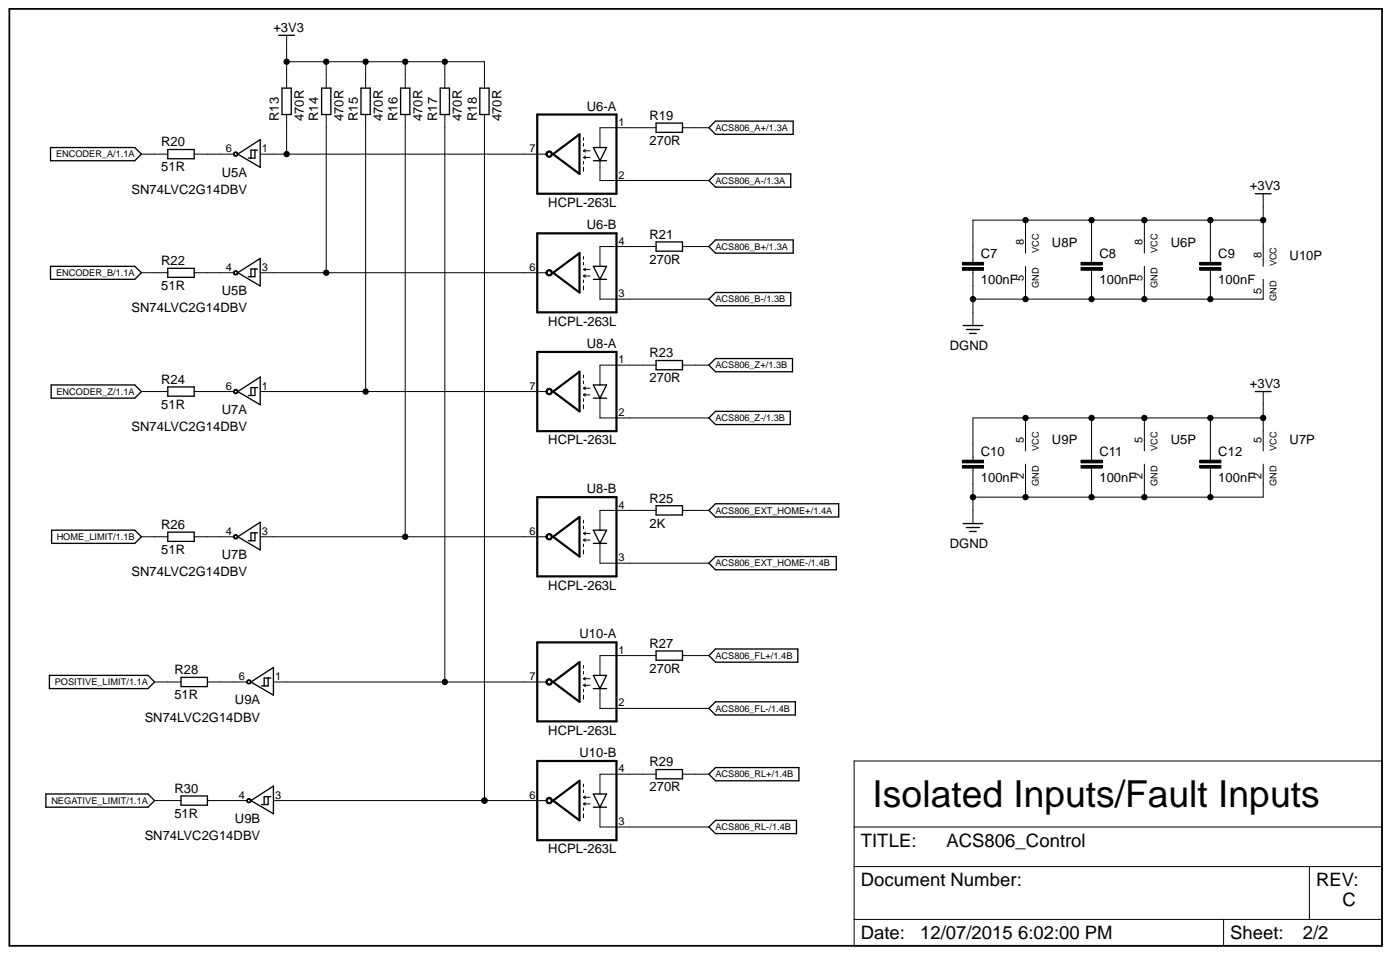
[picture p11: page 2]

Isolated Inputs/Fault Inputs

Document Number: | REV: C

Date: 12/07/2015 6:02:00 PM | Sheet: 2/2

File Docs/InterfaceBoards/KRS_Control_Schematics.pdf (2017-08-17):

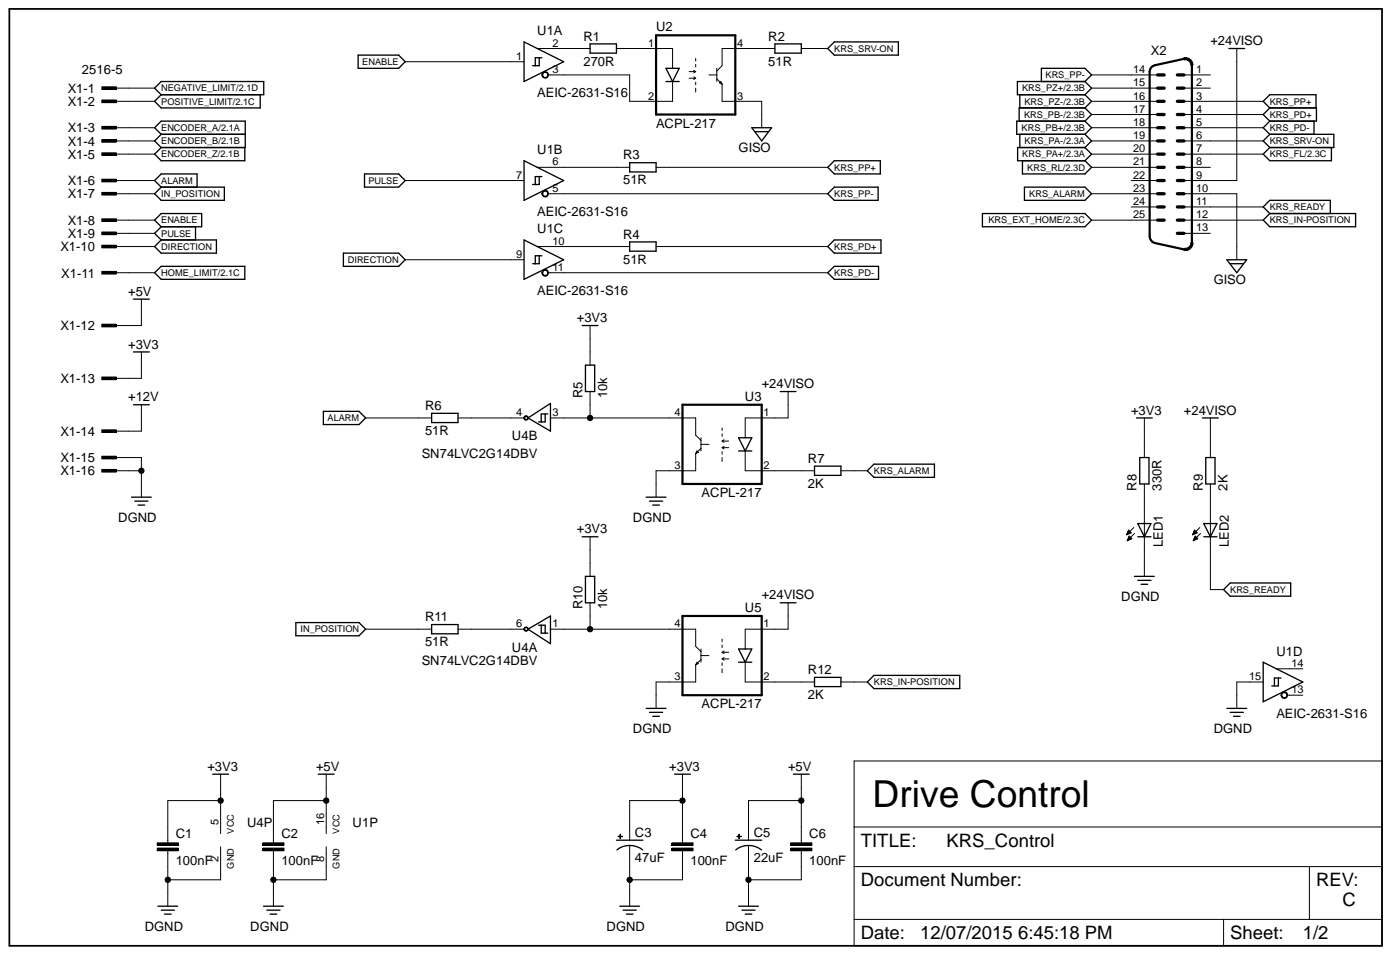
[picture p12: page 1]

Document Number: | REV: C

Date: 12/07/2015 6:45:18 PM | Sheet: 1/2


Document Number: | REV: C

Date: 12/07/2015 6:45:18 PM | Sheet: 2/2

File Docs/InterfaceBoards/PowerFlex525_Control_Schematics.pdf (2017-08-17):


Document Number: | REV: C

Date: 11/07/2015 4:53:55 PM | Sheet: 1/3


Isolated Outputs (VFD DIGIN)


Document Number: | REV: C

Date: 11/07/2015 4:53:55 PM | Sheet: 3/3




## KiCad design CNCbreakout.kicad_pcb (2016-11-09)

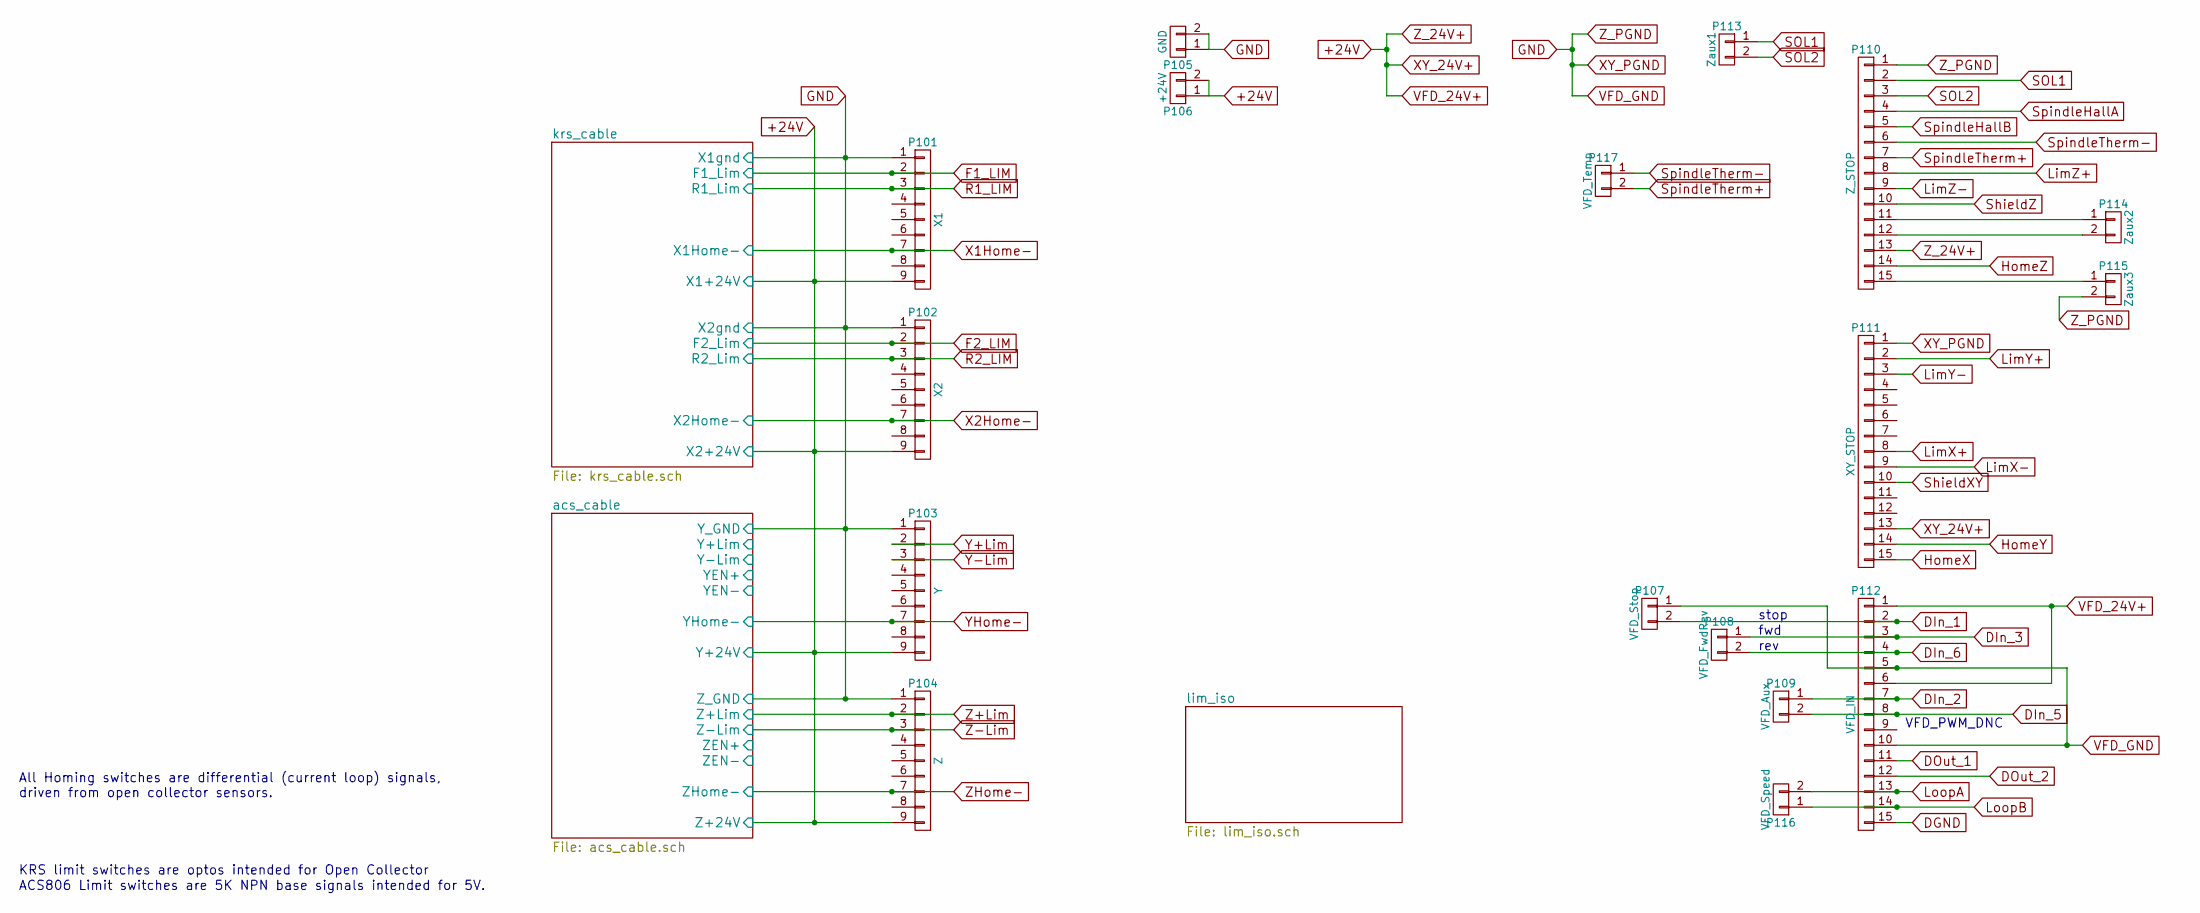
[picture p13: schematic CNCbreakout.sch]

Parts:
P101: X1; DE9FC
P102: X2; DE9FC
P103: Y; DE9FC
P104: Z; DE9FC
P105: GND; bornier2
P106: +24V; bornier2
P107: VFD_Stop; bornier2
P108: VFD_FwdRev; bornier2
P109: VFD_Aux; bornier2
P110: Z_STOP; DE15HDFC
P111: XY_STOP; DE15HDFC
P112: VFD_IN; DE15HDFC
P113: Zaux1; bornier2
P114: Zaux2; bornier2
P115: Zaux3; bornier2
P116: VFD_Speed; bornier2
P117: VFD_Temp; bornier2

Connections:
+24V: P101.9, P102.9, P103.9, P104.9, P106.1, P106.2, P110.13, P111.13, P112.1, P112.6; also elsewhere on the board
DGND: P112.15; also elsewhere on the board
DIn_1: P107.2, P112.2
DIn_2: P109.1, P112.7
DIn_3: P108.1, P112.3
DIn_5: P109.2, P112.8
DIn_6: P108.2, P112.4
DOut_1: P112.11; also elsewhere on the board
DOut_2: P112.12; also elsewhere on the board
F1_LIM: P101.2, P102.2; also elsewhere on the board
GND: P101.1, P102.1, P103.1, P104.1, P105.1, P105.2, P107.1, P110.1, P111.1, P112.5, P112.10, P115.2; also elsewhere on the board
HomeX: P101.7, P102.7, P111.15; also elsewhere on the board
HomeY: P103.7, P111.14; also elsewhere on the board
HomeZ: P104.7, P110.14; also elsewhere on the board
LimX+: P111.8; also elsewhere on the board
LimX-: P111.9; also elsewhere on the board
LimY+: P111.2; also elsewhere on the board
LimY-: P111.3; also elsewhere on the board
LimZ+: P110.8; also elsewhere on the board
LimZ-: P110.9; also elsewhere on the board
LoopA: P112.13, P116.2
LoopB: P112.14, P116.1
unnamed: P110.11, P114.1
unnamed: P110.12, P114.2
unnamed: P110.15, P115.1
R1_LIM: P101.3, P102.3; also elsewhere on the board
SOL1: P110.2, P113.1
SOL2: P110.3, P113.2
SpindleHallA: P110.4; also elsewhere on the board
SpindleHallB: P110.5; also elsewhere on the board
SpindleTherm+: P110.7, P117.2
SpindleTherm-: P110.6, P117.1
Y+Lim: P103.2; also elsewhere on the board
Y-Lim: P103.3; also elsewhere on the board
Z+Lim: P104.2; also elsewhere on the board
Z-Lim: P104.3; also elsewhere on the board

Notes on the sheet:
ACS806 Limit switches are 5K NPN base signals intended for 5V.
KRS limit switches are optos intended for Open Collector
All Homing switches are differential (current loop) signals, driven from open collector sensors.
stop
fwd
rev
VFD_PWM_DNC

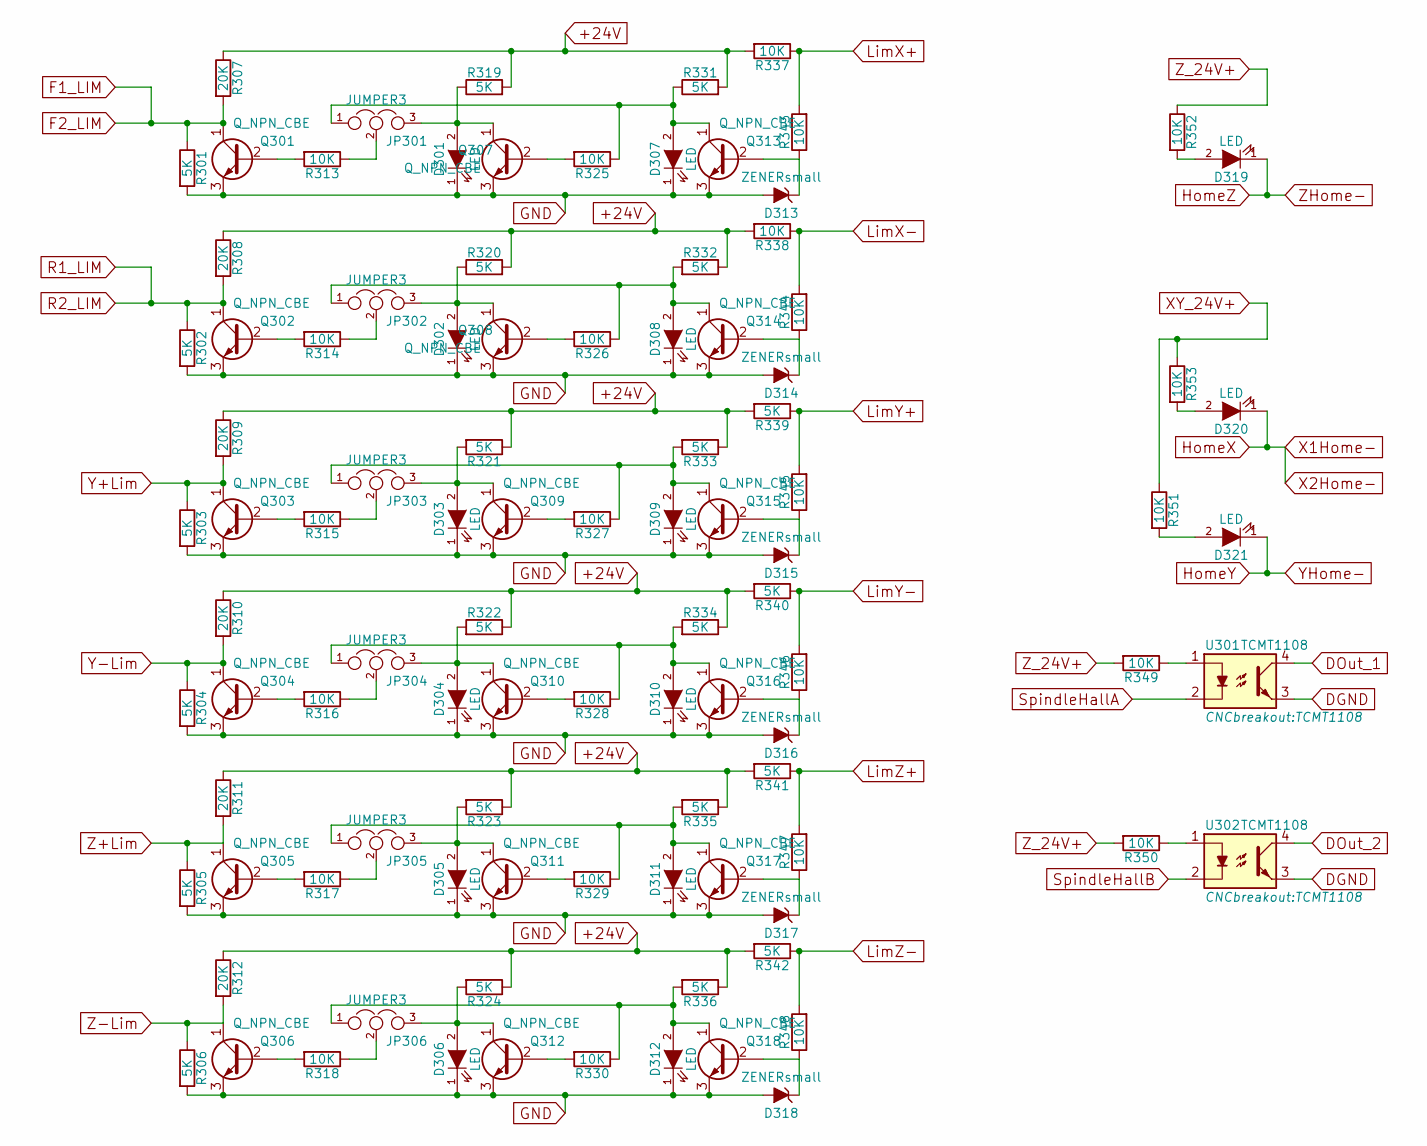
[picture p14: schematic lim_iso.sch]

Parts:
D301, D302, D303, D304, D305, D306, D307, D308, D309, D310, D311, D312, D319, D320, D321: LED; LED_1206
D313, D314, D315, D316, D317, D318: ZENERsmall; SOD-123
JP301, JP302, JP303, JP304, JP305, JP306: JUMPER3; JumperDouble
Q301, Q302, Q303, Q304, Q305, Q306, Q307, Q308, Q309, Q310, Q311, Q312, Q313, Q314, Q315, Q316, Q317, Q318: Q_NPN_CBE; SOT-23
R301, R302, R303, R304, R305, R306, R319, R320, R321, R322, R323, R324, R331, R332, R333, R334, R335, R336, R339, R340, R341, R342: 5K; R_1206
R307, R308, R309, R310, R311, R312: 20K; R_1206
R313, R314, R315, R316, R317, R318, R325, R326, R327, R328, R329, R330, R337, R338, R343, R344, R345, R346, R347, R348, R349, R350, R351, R352, R353: 10K; R_1206
U301, U302: TCMT1108

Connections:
+24V: R307.1, R308.1, R309.1, R310.1, R311.1, R312.1, R319.2, R320.2, R321.1, R322.1, R323.1, R324.1, R331.2, R332.1, R333.1, R334.1, R335.1, R336.1, R337.2, R338.2, R339.2, R340.2, R341.2, R342.2, R349.2, R350.2, R351.1, R352.1, R353.1; also elsewhere on the board
DGND: U301.3, U302.3; also elsewhere on the board
DOut_1: U301.4; also elsewhere on the board
DOut_2: U302.4; also elsewhere on the board
F1_LIM: Q301.1 (C), R301.1, R307.2; also elsewhere on the board
GND: D301.1 (K), D302.1 (K), D303.1 (K), D304.1 (K), D305.1 (K), D306.1 (K), D307.1 (K), D308.1 (K), D309.1 (K), D310.1 (K), D311.1 (K), D312.1 (K), D313.2 (A), D314.2 (A), D315.2 (A), D316.2 (A), D317.2 (A), D318.2 (A), Q301.3 (E), Q302.3 (E), Q303.3 (E), Q304.3 (E), Q305.3 (E), Q306.3 (E), Q307.3 (E), Q308.3 (E), Q309.3 (E), Q310.3 (E), Q311.3 (E), Q312.3 (E), Q313.3 (E), Q314.3 (E), Q315.3 (E), Q316.3 (E), Q317.3 (E), Q318.3 (E), R301.2, R302.2, R303.2, R304.2, R305.2, R306.2; also elsewhere on the board
HomeX: D320.1 (K); also elsewhere on the board
HomeY: D321.1 (K); also elsewhere on the board
HomeZ: D319.1 (K); also elsewhere on the board
LimX+: R337.1, R343.2; also elsewhere on the board
LimX-: R338.1, R344.2; also elsewhere on the board
LimY+: R339.1, R345.2; also elsewhere on the board
LimY-: R340.1, R346.2; also elsewhere on the board
LimZ+: R341.1, R347.2; also elsewhere on the board
LimZ-: R342.1, R348.2; also elsewhere on the board
unnamed: D301.2 (A), JP301.3, Q307.1 (C), R319.1
unnamed: D302.2 (A), JP302.3, Q308.1 (C), R320.1
unnamed: D303.2 (A), JP303.3, Q309.1 (C), R321.2
unnamed: D304.2 (A), JP304.3, Q310.1 (C), R322.2
unnamed: D305.2 (A), JP305.3, Q311.1 (C), R323.2
unnamed: D306.2 (A), JP306.3, Q312.1 (C), R324.2
unnamed: D307.2 (A), JP301.1, Q313.1 (C), R325.1, R331.1
unnamed: D308.2 (A), JP302.1, Q314.1 (C), R326.1, R332.2
unnamed: D309.2 (A), JP303.1, Q315.1 (C), R327.1, R333.2
unnamed: D310.2 (A), JP304.1, Q316.1 (C), R328.1, R334.2
unnamed: D311.2 (A), JP305.1, Q317.1 (C), R329.1, R335.2
unnamed: D312.2 (A), JP306.1, Q318.1 (C), R330.1, R336.2
unnamed: D313.1 (K), Q313.2 (B), R343.1
unnamed: D314.1 (K), Q314.2 (B), R344.1
unnamed: D315.1 (K), Q315.2 (B), R345.1
unnamed: D316.1 (K), Q316.2 (B), R346.1
unnamed: D317.1 (K), Q317.2 (B), R347.1
unnamed: D318.1 (K), Q318.2 (B), R348.1
unnamed: D319.2 (A), R352.2
unnamed: D320.2 (A), R353.2
unnamed: D321.2 (A), R351.2
unnamed: JP301.2, R313.1
unnamed: JP302.2, R314.1
unnamed: JP303.2, R315.1
unnamed: JP304.2, R316.1
unnamed: JP305.2, R317.1
unnamed: JP306.2, R318.1
unnamed: Q301.2 (B), R313.2
unnamed: Q302.2 (B), R314.2
unnamed: Q303.2 (B), R315.2
unnamed: Q304.2 (B), R316.2
unnamed: Q305.2 (B), R317.2
unnamed: Q306.2 (B), R318.2
unnamed: Q307.2 (B), R325.2
unnamed: Q308.2 (B), R326.2
unnamed: Q309.2 (B), R327.2
unnamed: Q310.2 (B), R328.2
unnamed: Q311.2 (B), R329.2
unnamed: Q312.2 (B), R330.2
unnamed: R349.1, U301.1
unnamed: R350.1, U302.1
R1_LIM: Q302.1 (C), R302.1, R308.2; also elsewhere on the board
SpindleHallA: U301.2; also elsewhere on the board
SpindleHallB: U302.2; also elsewhere on the board
Y+Lim: Q303.1 (C), R303.1, R309.2; also elsewhere on the board
Y-Lim: Q304.1 (C), R304.1, R310.2; also elsewhere on the board
Z+Lim: Q305.1 (C), R305.1, R311.2; also elsewhere on the board
Z-Lim: Q306.1 (C), R306.1, R312.2; also elsewhere on the board

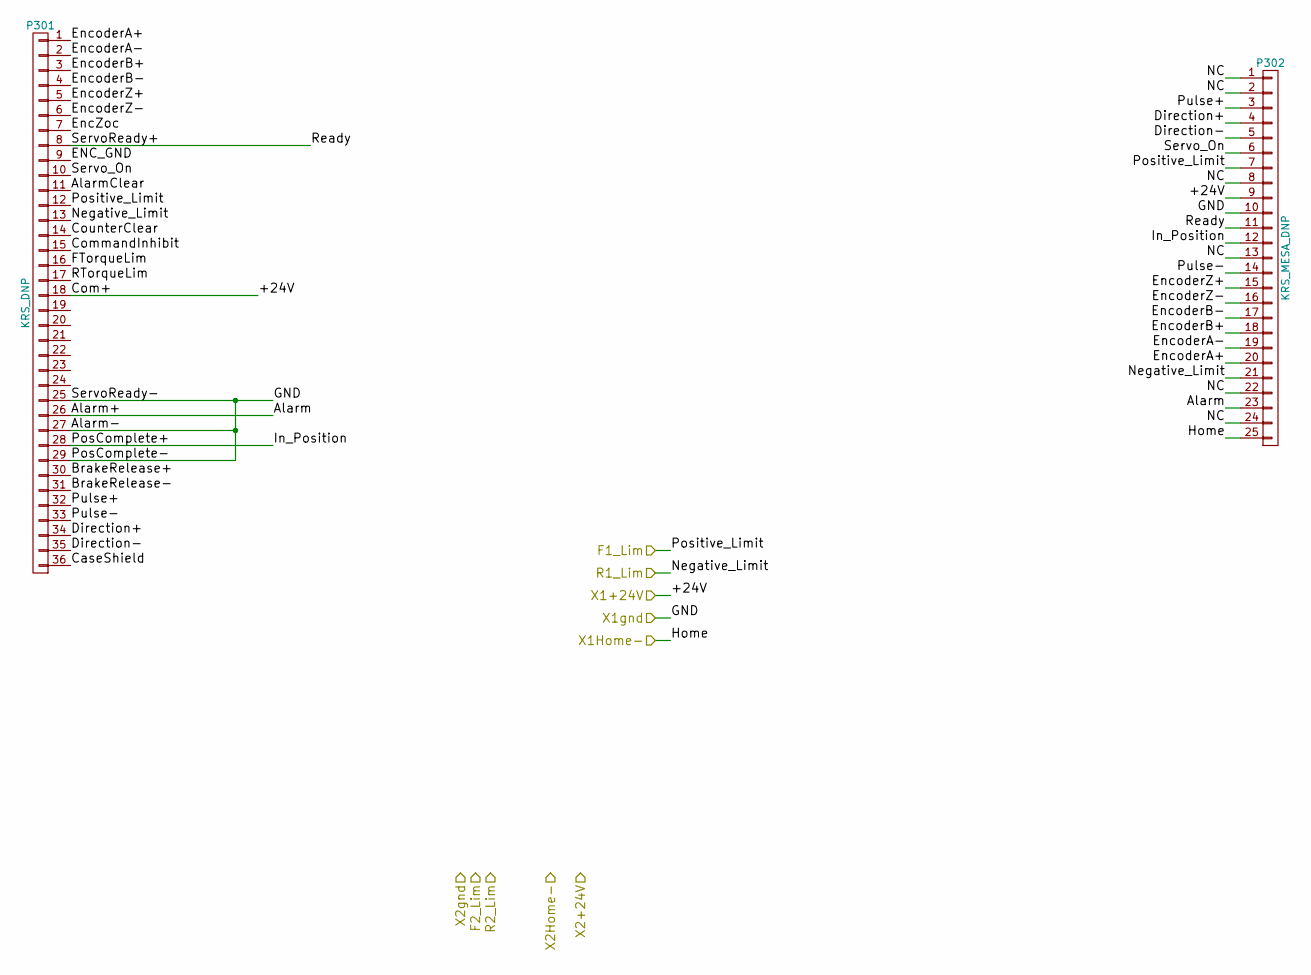
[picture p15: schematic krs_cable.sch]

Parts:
P301: KRS_DNP
P302: KRS_MESA_DNP

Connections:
unnamed: P301.1, P302.20
unnamed: P301.2, P302.19
unnamed: P301.3, P302.18
unnamed: P301.4, P302.17
unnamed: P301.5, P302.15
unnamed: P301.6, P302.16
unnamed: P301.8, P302.11
unnamed: P301.10, P302.6
unnamed: P301.12, P302.7
unnamed: P301.13, P302.21
unnamed: P301.18, P302.9
unnamed: P301.25, P301.27, P301.29, P302.10
unnamed: P301.26, P302.23
unnamed: P301.28, P302.12
unnamed: P301.32, P302.3
unnamed: P301.33, P302.14
unnamed: P301.34, P302.4
unnamed: P301.35, P302.5
unnamed: P302.1, P302.2, P302.8, P302.13, P302.22, P302.24

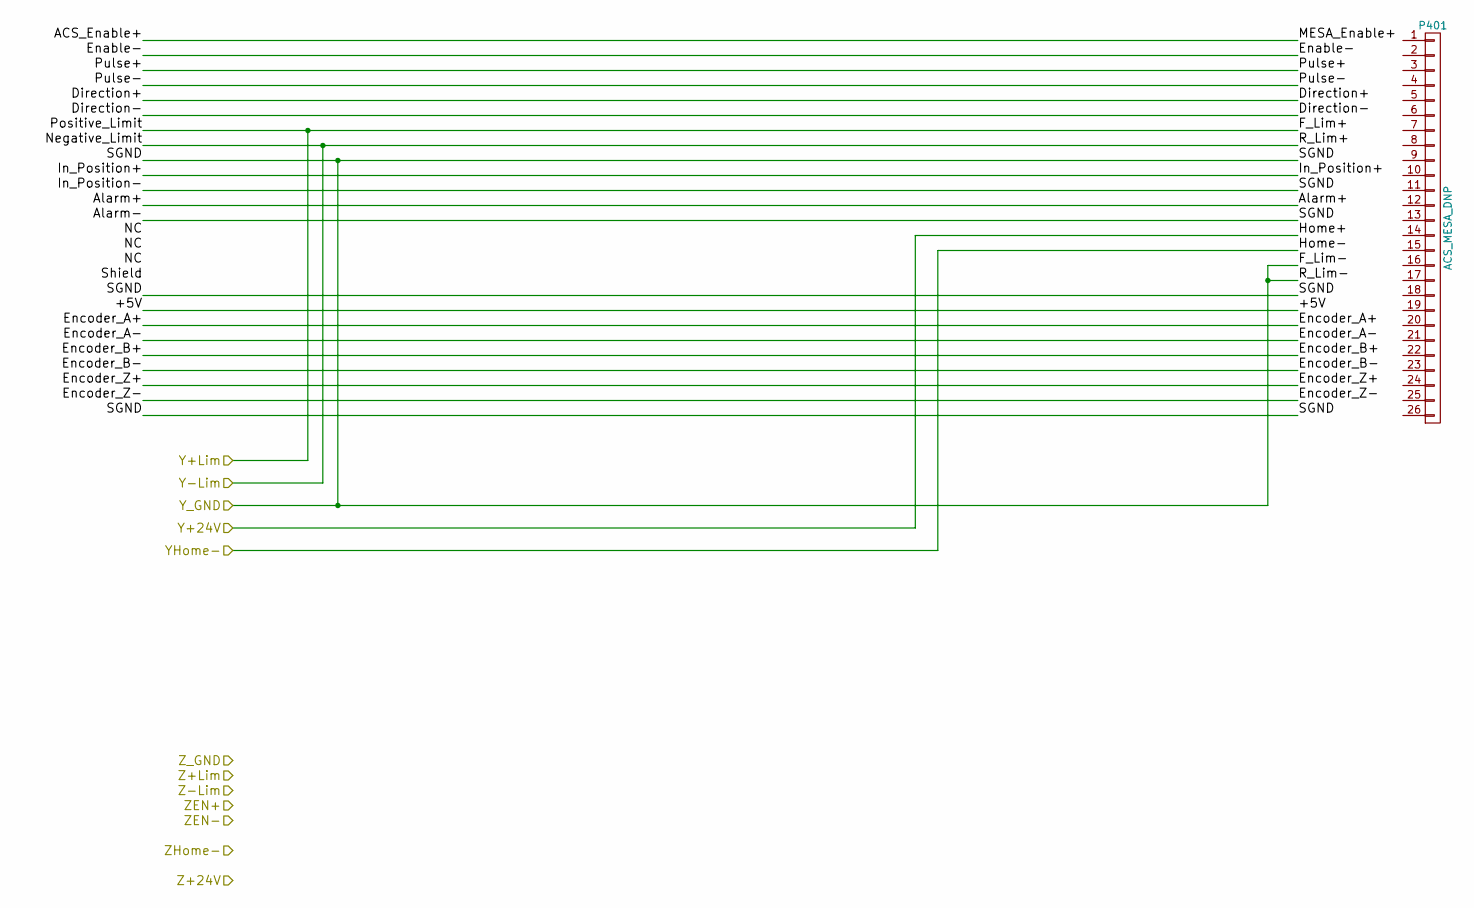
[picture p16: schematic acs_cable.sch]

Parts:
P401: ACS_MESA_DNP

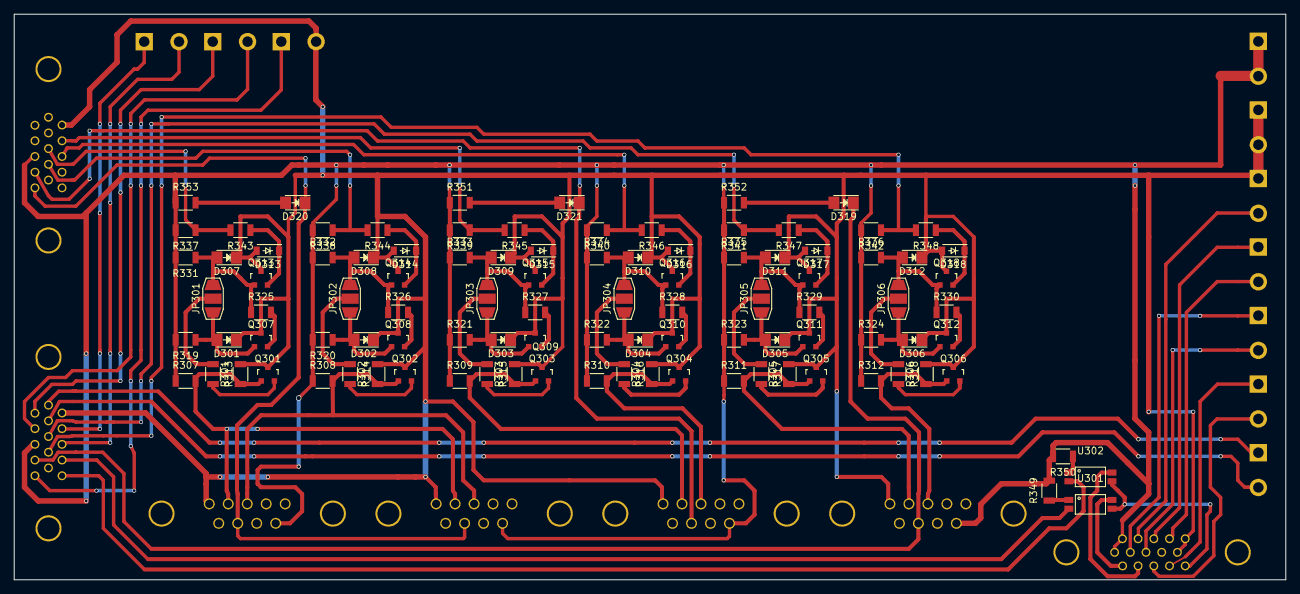
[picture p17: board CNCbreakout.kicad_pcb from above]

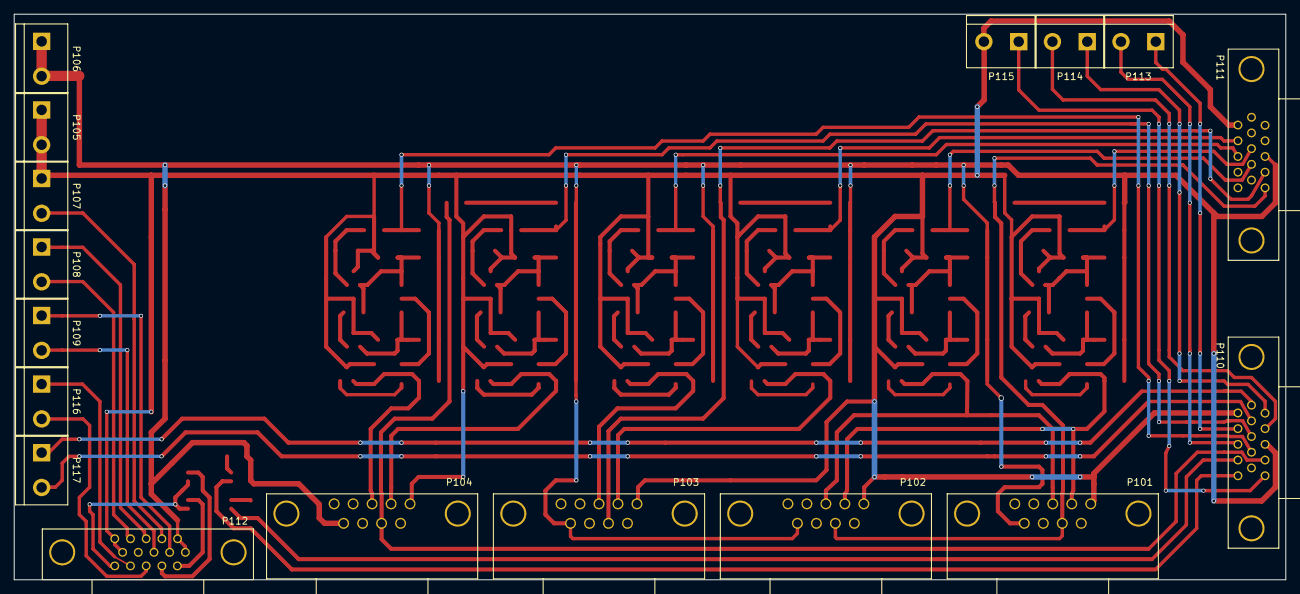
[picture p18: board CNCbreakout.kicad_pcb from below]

Board: 2 copper layers, 185.5 x 82.5 mm, 117 parts (17 on the bottom side), 77 nets.

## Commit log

2016-07-12 Most pinouts done
    [CNCbreakout.kicad_pcb, CNCbreakout.sch]
2016-07-15 added spindle hall, assignd footprints
    [CNCbreakout.sch]
2016-07-22 cleanup and added enable intercept
    [CNCbreakout.sch, Estop.sch, acs_cable.sch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]
2016-08-18 started pcb layout
    [CNCbreakout.kicad_pcb, CNCbreakout.sch, lim_iso.sch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]
2016-08-22 added opto and DE footprints
    [CNCbreakout.kicad_pcb, CNCbreakout.sch, Estop.sch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]
2016-09-19 set limits to pull down, optional invert
    [CNCbreakout.kicad_pcb, CNCbreakout.sch, acs_cable.sch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]
2016-09-22 closer to full routing
    [CNCbreakout.kicad_pcb]
2016-10-10 adjusted DE15 footprint, added aux Z-stage lines
    [CNCbreakout.kicad_pcb, CNCbreakout.sch]
2016-10-10 added thermistor
    [CNCbreakout.kicad_pcb, CNCbreakout.sch, Estop.sch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]
2016-10-10 full route
    [CNCbreakout.kicad_pcb]
2016-10-24 added enable input connector
    [CNCbreakout.kicad_pcb, CNCbreakout.sch, Estop.sch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]
2016-11-09 checked limits and homes, removed enable, adjusted routing
    [CNCbreakout.kicad_pcb, CNCbreakout.sch, acs_cable.sch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]
2017-03-02 added documents and a readme
    [5i22_Baseboard_RevC.GBL, 5i22_Baseboard_RevC.GBO, 5i22_Baseboard_RevC.GBP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]
2017-08-17 exported PDFs of the schematics
